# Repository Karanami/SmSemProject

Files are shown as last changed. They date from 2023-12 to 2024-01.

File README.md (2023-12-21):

# Piotr Lesicki 151052 - Line Follower

## General description
Line Follower - as it's name implies this robot will realise the task of following the line. 
The robot will consist of two motors, imu, line sensors (white/black color detectors), motor
encoders as well as an external data storage (flash/sd card) for data logging and of coures
it will also have an uC for general control.

## Hardware

### Motors & motor encoders
The robot will use a simple brushed motor with an extended shaft for the encoder feedback

### IMU
A six axis IMU will be used for data logging.

### line sensors
Basic refleted light detectors will be used for estimating where a black line on a white
background is.

### External data storage
A external storage in a form of a chip or a sd card will be used for logging

### uC
An STM32WB55RGVx will be used for the heart of the robot. It will also allow for a bluetooth
communication implementation to be included in the project, making the whole project smaller 
and more compact.

## Line Following task - regulator
The appropriate regulator is yet to be chosen

## Software

### RTOS 
For an easier implementation of software a fitting RTOS will be used. Azure RTOS will be used 
for that since it implements many robust sub-libraries allowing for light-weight aplications,
such as storage (file storage) drivers for external flash/sd cards or usb interfaces allowing
for on slave multiple devices implemantation and much more.
<br/> 

## Examples
- https://forbot.pl/blog/leksykon/robot-typu-linefollower
- https://www.jsumo.com/arduino-pid-based-line-follower-kit1

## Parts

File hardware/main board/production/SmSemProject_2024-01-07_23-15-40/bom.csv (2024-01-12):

Designator | Footprint | Quantity | Value | LCSC Part #
ANT1 | 74889302450 | 1 | 74889302450
C1, C2 | 0603 | 2 | 20pF
C10 | 0603 | 1 | 100pF
C11, C16, C19, C25, C26, C27, C28, C3, C30, C31, C4, C5, C9 | 0603 | 13 | 100nF
C13 | 0603 | 1 | 10uF
C14, C15, C18, C24 | 0603 | 4 | 4.7uF
C17, C29 | CP_Elec_5x4.5 | 2 | 100uF
C20 | 0603 | 1 | 0.3pF
C21 | 0603 | 1 | 0.8pF
C7 | 0603 | 1 | 10nF
C8 | 0603 | 1 | 1uF
D1, D3 | D_SOD-128 | 2 | RBS2LAM40CTR
D2, D4, D5, D6, D7, D8 | 0603 | 6 | LED_Small
F1, F2 | 1210 | 2 | 0.5A/16V
FL1 | DLF162500LT5028A1 | 1 | DLF162500LT-5028A1
H1, H2, H3, H4 | MountingHole_3.2mm_M3_Pad_Via | 4 | MountingHole_Pad
IC1 | QFN40P800X800X100-69N-D | 1 | STM32WB55RGV6
IC2, IC3 | SON50P200X200X80-9N | 2 | DRV8212PDSGR
IC4 | SON127P800X600X80-9N-D | 1 | W25N01GVZEIG
IC5 | LSM6DSLTR | 1 | LSM6DSLTR
IC6, IC7 | SOT-23-6 | 2 | SN74LVC1G18DBVRG4
J1, J2 | JST_SH_BM06B-SRSS-TB_1x06-1MP_P1.00mm_Vertical | 2 | JST-SH 01x06
J3 | JST_XH_B3B-XH-A_1x03_P2.50mm_Vertical | 1 | JST_XH_B3B
J4 | FTSH-107-XX-YYY-DV-K-A | 1 | FTSH-107-01-L-DV-K-A
J6 | USB4145030070C | 1 | USB4145-03-0070-C
J7 | Molex_200528-0100_1x10-1MP_P1.00mm_Horizontal | 1 | Conn_01x10
L1 | 1206 | 1 | 1mH
L2 | WE-PMI_080562 | 1 | 74479774222
L3 | 0603 | 1 | 2.7nH
R1 | 0603 | 1 | 1k
R10, R11, R12, R4, R5, R6, R7, R8, R9 | 0603 | 9 | 10k
R2, R3 | 0603 | 2 | 5.1k
U1 | SOT-223-3_TabPin2 | 1 | LM1117MP-3.3
U2 | SOT-23-6 | 1 | USBLC6-2SC6
Y1 | Crystal_SMD_3225-4Pin_3.2x2.5mm | 1 | X322516MLB4SI

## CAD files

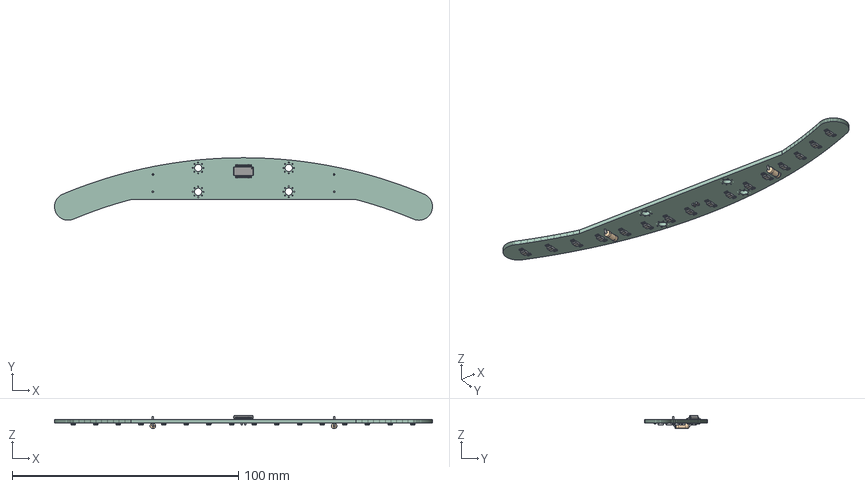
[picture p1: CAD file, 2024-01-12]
hardware/front board/SmSemProject-FrontBoard.step
166.9 x 27.6 x 5.95 mm
PCB

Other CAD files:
cad/podłoga1^całość.SLDPRT

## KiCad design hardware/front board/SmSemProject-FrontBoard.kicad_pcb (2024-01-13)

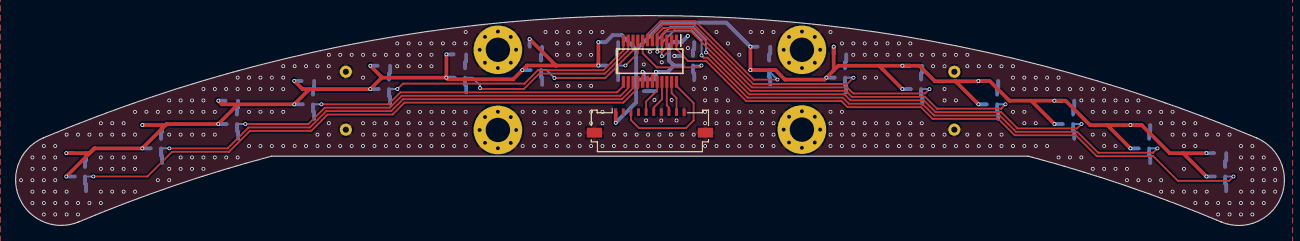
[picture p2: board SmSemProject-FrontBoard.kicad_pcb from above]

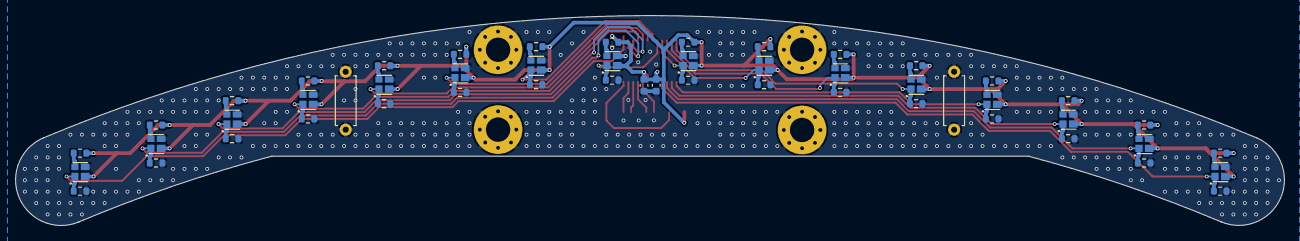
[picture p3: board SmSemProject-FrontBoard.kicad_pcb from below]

Board: 2 copper layers, 166.9 x 27.6 mm, 58 parts (52 on the bottom side), 39 nets.

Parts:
C1, C2: 100nF; C_0603_1608Metric
H1, H2, H3, H4: MountingHole_Pad; MountingHole_3.2mm_M3_Pad_Via
IC1, IC3, IC4, IC5, IC6, IC7, IC8, IC9, IC10, IC11, IC12, IC13, IC14, IC15, IC16, IC17: VCNT2020
IC2: MAX11643EEG+; SOP64P602X175-24N
J2: Conn_01x10_MountingPin; Molex_200528-0100_1x10-1MP_P1.00mm_Horizontal
R1, R3, R5, R7, R9, R11, R13, R15, R17, R19, R21, R23, R25, R27, R29, R31: 1k; R_0603_1608Metric
R2, R4, R6, R8, R10, R12, R14, R16, R18, R20, R22, R24, R26, R28, R30, R32: 100; R_0603_1608Metric
R33, R34: --; R_Axial_DIN0207_L6.3mm_D2.5mm_P7.62mm_Horizontal

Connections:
+3.3V: C1.2, C2.2, IC1.2, IC2.17 (REF), IC2.19 (VDD), IC3.2, IC4.2, IC5.2, IC6.2, IC7.2, IC8.2, IC9.2, IC10.2, IC11.2, IC12.2, IC13.2, IC14.2, IC15.2, IC16.2, IC17.2, J2.1, R2.2, R4.2, R6.2, R8.2, R10.2, R12.2, R14.2, R16.2, R18.2, R20.2, R22.2, R24.2, R26.2, R28.2, R30.2, R32.2
/OUT0: IC1.1, IC2.1 (AIN0), R1.1
/OUT1: IC2.2 (AIN1), IC3.1, R3.1
/OUT2: IC2.3 (AIN2), IC4.1, R5.1
/OUT3: IC2.4 (AIN3), IC5.1, R7.1
/OUT4: IC2.5 (AIN4), IC7.1, R11.1
/OUT5: IC2.6 (AIN5), IC8.1, R13.1
/OUT6: IC2.7 (AIN6), IC9.1, R15.1
/OUT7: IC2.8 (AIN7), IC6.1, R9.1
/OUT8: IC2.9 (AIN8), IC11.1, R19.1
/OUT9: IC2.10 (AIN9), IC12.1, R21.1
/OUT10: IC2.11 (AIN10), IC13.1, R23.1
/OUT11: IC2.12 (AIN11), IC10.1, R17.1
/OUT12: IC2.13 (AIN12), IC15.1, R27.1
/OUT13: IC2.14 (AIN13), IC16.1, R29.1
/OUT14: IC2.15 (AIN14), IC17.1, R31.1
/OUT15: IC2.16 (~CNVST/AIN15), IC14.1, R25.1
/SPI_CLK: IC2.21 (SCLK), J2.6
/SPI_EX_INT1: IC2.24 (~EOC), J2.3
/SPI_MISO: IC2.23 (DOUT), J2.9
/SPI_MOSI: IC2.22 (DIN), J2.8
/Sensor0/A: IC1.3 (A), R2.1
/Sensor1/A: IC3.3 (A), R4.1
/Sensor2/A: IC4.3 (A), R6.1
/Sensor3/A: IC5.3 (A), R8.1
/Sensor4/A: IC7.3 (A), R12.1
/Sensor5/A: IC8.3 (A), R14.1
/Sensor6/A: IC9.3 (A), R16.1
/Sensor7/A: IC6.3 (A), R10.1
/Sensor8/A: IC11.3 (A), R20.1
/Sensor9/A: IC12.3 (A), R22.1
/Sensor10/A: IC13.3 (A), R24.1
/Sensor11/A: IC10.3 (A), R18.1
/Sensor12/A: IC15.3 (A), R28.1
/Sensor13/A: IC16.3 (A), R30.1
/Sensor14/A: IC17.3 (A), R32.1
/Sensor15/A: IC14.3 (A), R26.1
/~SPI_EX1_CS: IC2.20 (~CS), J2.5
GND: C1.1, C2.1, H1.1, H2.1, H3.1, H4.1, IC1.4 (K), IC2.18 (GND), IC3.4 (K), IC4.4 (K), IC5.4 (K), IC6.4 (K), IC7.4 (K), IC8.4 (K), IC9.4 (K), IC10.4 (K), IC11.4 (K), IC12.4 (K), IC13.4 (K), IC14.4 (K), IC15.4 (K), IC16.4 (K), IC17.4 (K), J2.7, J2.10, J2.MP (MountPin), R1.2, R3.2, R5.2, R7.2, R9.2, R11.2, R13.2, R15.2, R17.2, R19.2, R21.2, R23.2, R25.2, R27.2, R29.2, R31.2, R33.1, R33.2, R34.1, R34.2

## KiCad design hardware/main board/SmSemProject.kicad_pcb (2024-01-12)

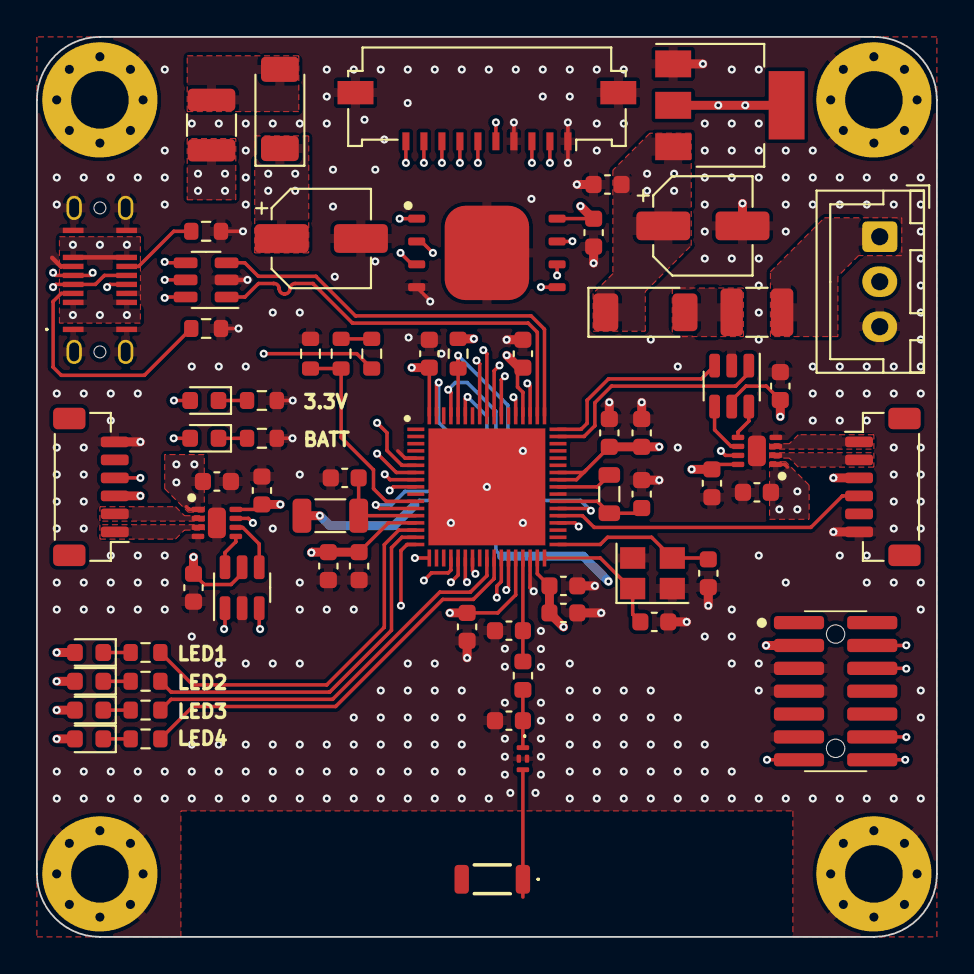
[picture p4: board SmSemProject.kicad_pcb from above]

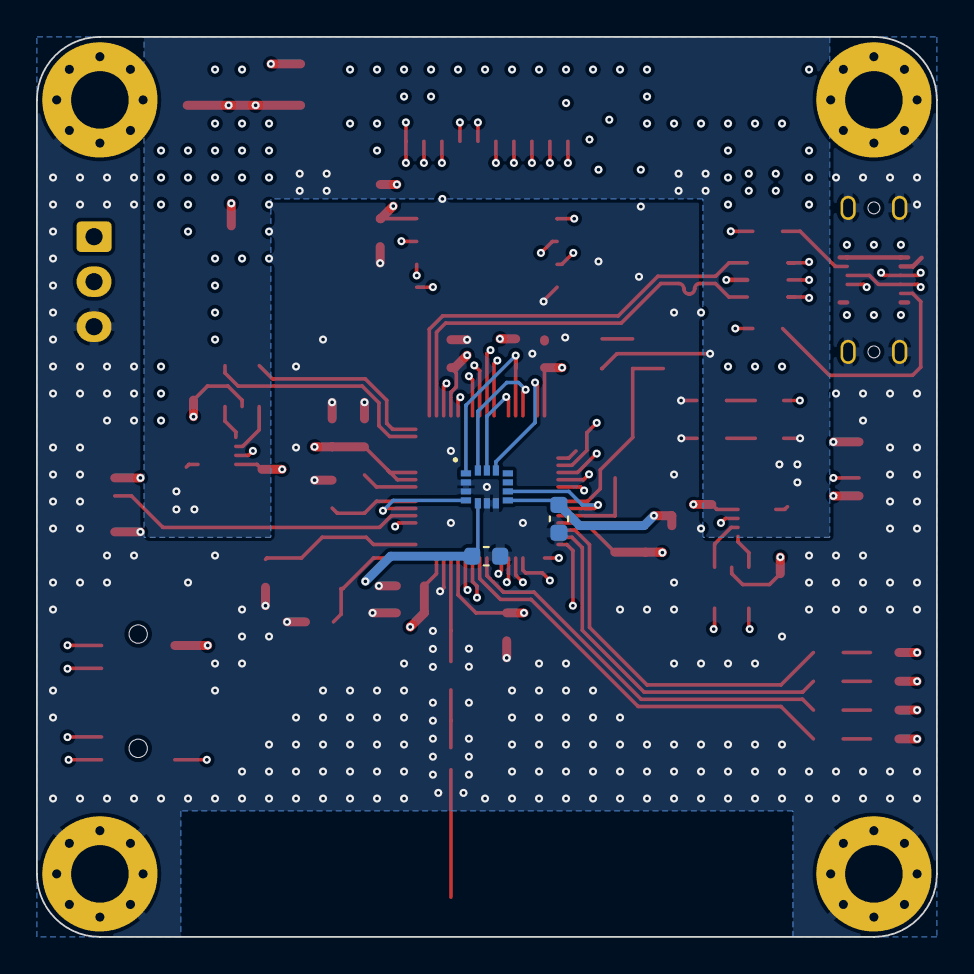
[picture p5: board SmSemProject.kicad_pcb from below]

Board: 8 copper layers, 50.0 x 50.0 mm, 74 parts (3 on the bottom side), 69 nets.

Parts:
ANT1: 74889302450
C1, C2: 20pF; C_0603_1608Metric
C3, C4, C5, C9, C11, C16, C19, C25, C26, C27, C28, C30, C31: 100nF; C_0603_1608Metric
C7: 10nF; C_0603_1608Metric
C8: 1uF; C_0603_1608Metric
C10: 100pF; C_0603_1608Metric
C13: 10uF; C_0603_1608Metric
C14, C15, C18, C24: 4.7uF; C_0603_1608Metric
C17, C29: 100uF; CP_Elec_5x4.5
C20: 0.3pF; C_0603_1608Metric
C21: 0.8pF; C_0603_1608Metric
D1, D3: RBS2LAM40CTR; D_SOD-128
D2, D4, D5, D6, D7, D8: LED_Small; LED_0603_1608Metric
F1, F2: 0.5A/16V; Fuse_1210_3225Metric
FL1: DLF162500LT-5028A1; DLF162500LT5028A1
H1, H2, H3, H4: MountingHole_Pad; MountingHole_3.2mm_M3_Pad_Via
IC1: STM32WB55RGV6; QFN40P800X800X100-69N-D
IC2, IC3: DRV8212PDSGR; SON50P200X200X80-9N
IC4: W25N01GVZEIG; SON127P800X600X80-9N-D
IC5: LSM6DSLTR
IC6, IC7: SN74LVC1G18DBVRG4; SOT-23-6
J1, J2: JST-SH 01x06; JST_SH_BM06B-SRSS-TB_1x06-1MP_P1.00mm_Vertical
J3: JST_XH_B3B; JST_XH_B3B-XH-A_1x03_P2.50mm_Vertical
J4: FTSH-107-01-L-DV-K-A; FTSH-107-XX-YYY-DV-K-A
J6: USB4145-03-0070-C; USB4145030070C
J7: Conn_01x10; Molex_200528-0100_1x10-1MP_P1.00mm_Horizontal
L1: 1mH; L_1206_3216Metric
L2: 74479774222; WE-PMI_080562
L3: 2.7nH; L_0603_1608Metric
R1: 1k; R_0603_1608Metric
R2, R3: 5.1k; R_0603_1608Metric
R4, R5, R6, R7, R8, R9, R10, R11, R12: 10k; R_0603_1608Metric
U1: LM1117MP-3.3; SOT-223-3_TabPin2
U2: USBLC6-2SC6; SOT-23-6
Y1: X322516MLB4SI; Crystal_SMD_3225-4Pin_3.2x2.5mm

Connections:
+3.3V: C3.2, C4.2, C5.2, C7.1, C8.1, C9.2, C10.2, C11.2, C15.1, C19.1, C25.1, C26.1, C27.2, C28.2, C30.1, C31.1, D2.2 (A), D4.2 (A), D5.2 (A), D6.2 (A), D7.2 (A), IC1.14 (VDDA), IC1.30 (VDD), IC1.33 (VDDRF), IC1.44 (VDDSMPS), IC1.45 (VDD), IC1.55 (VDDUSB), IC1.68 (VDD), IC2.8 (VCC), IC3.8 (VCC), IC4.8 (VCC), IC5.5 (VDDIO), IC5.8 (VDD), IC6.5 (VCC), IC7.5 (VCC), J1.3, J2.3, J4.3, J7.10, L1.1, R1.1, U1.2 (VO)
+BATT: C16.1, C17.1, C18.1, C24.1, C29.1, D1.1 (K), D3.1 (K), D8.2 (A), IC2.1 (VM), IC3.1 (VM), R9.2, U1.3 (VI)
/ANT_IN: ANT1.1 (FEED), FL1.3 (OUT)
/CONN_D+: J6.A6 (D+), J6.B6 (D+), U2.6 (I/O1)
/CONN_D-: J6.A7 (D-), J6.B7 (D-), U2.4 (I/O2)
/FLT_IN: C21.2, FL1.1 (IN), L3.2
/M_LEFT+: IC2.3 (OUT2), J2.1
/M_LEFT-: IC2.2 (OUT1), J2.2
/M_LEFT_A: IC1.9 (PC0), J2.4
/M_LEFT_DIRECTION: IC1.24 (PA9), IC7.1
/M_LEFT_PWM: IC1.23 (PA8), IC7.3
/M_RIGHT+: IC3.3 (OUT2), J1.1
/M_RIGHT-: IC3.2 (OUT1), J1.2
/M_RIGHT_A: IC1.39 (PB1), J1.4
/M_RIGHT_DIRECTION: IC1.50 (PC6), IC6.1
/M_RIGHT_PWM: IC1.51 (PA10), IC6.3
/Motor Control Left/PWMF: IC2.6 (IN1), IC7.4
/Motor Control Left/PWMR: IC2.5 (IN2), IC7.6
/Motor Control Left/~SLEEP: IC1.38 (PB0), IC2.7 (~SLEEP), IC3.7 (~SLEEP)
/Motor Control Right/PWMF: IC3.6 (IN1), IC6.4
/Motor Control Right/PWMR: IC3.5 (IN2), IC6.6
/SPI_CLK: IC1.63 (PB3), IC5.13 (SCL), J7.5
/SPI_EX_INT1: IC1.60 (PC12), J7.8
/SPI_EX_INT2: IC1.61 (PD0), J7.9
/SPI_MISO: IC1.64 (PB4), IC5.1 (SDO/SA0), J7.2, R1.2
/SPI_MOSI: IC1.65 (PB5), IC5.14 (SDI/SDA), J7.3
/VBUS: F2.1, J6.A4 (VBUS), J6.A9 (VBUS), J6.B4 (VBUS), J6.B9 (VBUS), U2.5 (VBUS)
/VBUSFUSE: D3.2 (A), F2.2
/VCONN: F1.2, J3.1
/VFUSE: D1.2 (A), F1.1
/uC/ANT_OUT: C20.1, IC1.31 (RF1), L3.1
/uC/D+: IC1.53 (PA12), U2.1 (I/O1)
/uC/D-: IC1.52 (PA11), U2.3 (I/O2)
/uC/IMU_INT1: IC1.12 (PC3), IC5.9 (INT2)
/uC/IMU_INT2: IC1.40 (PE4), IC5.4 (INT1)
/uC/LED1: IC1.15 (PA0), R5.1
/uC/LED2: IC1.16 (PA1), R6.1
/uC/LED3: IC1.26 (PC5), R7.1
/uC/LED4: IC1.27 (PB2), R8.1
/uC/OSC_IN: C1.2, IC1.35 (OSC_IN), Y1.3
/uC/OSC_OUT: C2.1, IC1.34 (OSC_OUT), Y1.1
/uC/QSPI_CLK: IC1.18 (PA3), IC4.6 (CLK)
/uC/QSPI_IO0: IC1.7 (PB9), IC4.5 (DI(IO0))
/uC/QSPI_IO1: IC1.6 (PB8), IC4.2 (DO(IO1))
/uC/QSPI_IO2: IC1.22 (PA7), IC4.3 (~WP(IO2))
/uC/QSPI_IO3: IC1.21 (PA6), IC4.7 (~HOLD(IO3))
/uC/SWCLK: IC1.56 (PA14), J4.6
/uC/SWDIO: IC1.54 (PA13), J4.4
/uC/UART_RX: IC1.28 (PB10), J4.13
/uC/UART_TX: IC1.29 (PB11), J4.14
/uC/VBAT: IC1.11 (PC2), R10.2, R11.1
/uC/VFBSMPS: C14.1, IC1.41 (VFBSMPS), L2.2
/uC/VLXSMPS: IC1.43 (VLXSMPS), L2.1
/uC/VREF+: C13.2, IC1.13 (VREF+), L1.2
/uC/~QSPI_CS: IC1.17 (PA2), IC4.1 (~CS)
/uC/~RST: IC1.8 (~RST), J4.12
/uC/~SPI_IMU_CS: IC1.67 (PB7), IC5.12 (~CS)
/~SPI_EX1_CS: IC1.58 (PC10), J7.6
/~SPI_EX2_CS: IC1.59 (PC11), J7.7
GND: C1.1, C2.2, C3.1, C4.1, C5.1, C7.2, C8.2, C9.1, C10.1, C11.1, C13.1, C14.2, C15.2, C16.2, C17.2, C18.2, C19.2, C20.2, C21.1, C24.2, C25.2, C26.2, C27.1, C28.1, C29.2, C30.2, C31.2, FL1.2 (GND), FL1.4 (GND), H1.1, H2.1, H3.1, H4.1, IC1.5 (PH3-BOOT0), IC1.32 (VSSRF), IC1.42 (VSSSMPS), IC1.69 (EP), IC2.4 (GND), IC2.9 (EP), IC3.4 (GND), IC3.9 (EP), IC4.4 (GND), IC4.9 (EP), IC5.2 (SDX), IC5.3 (SCX), IC5.6 (GND), IC5.7 (GND), IC6.2 (GND), IC7.2 (GND), J1.6, J2.6, J3.3, J4.5, J4.7, J4.11, J6.A1 (GND), J6.A8 (SBU1), J6.A12 (GND), J6.B1 (GND), J6.B8 (SBU2), J6.B12 (GND), J6.MH (SHIELD), J7.1, J7.4, J7.MP (MountPin), R2.2, R3.2, R4.1, R10.1, R12.1, U1.1 (GND), U2.2 (GND), Y1.2, Y1.4
unnamed: D2.1 (K), R4.2
unnamed: D4.1 (K), R5.2
unnamed: D5.1 (K), R6.2
unnamed: D6.1 (K), R7.2
unnamed: D7.1 (K), R8.2
unnamed: D8.1 (K), R12.2
unnamed: J6.A5 (CC1), R2.1
unnamed: J6.B5 (CC2), R3.1
unnamed: R9.1, R11.2

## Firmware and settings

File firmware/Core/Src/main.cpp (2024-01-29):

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
/* Includes ------------------------------------------------------------------*/
#include "main.h"
#include "cmsis_os.h"
#include "adc.h"
#include "dma.h"
#include "ipcc.h"
#include "lptim.h"
#include "usart.h"
#include "memorymap.h"
#include "quadspi.h"
#include "rf.h"
#include "rtc.h"
#include "spi.h"
#include "tim.h"
#include "usb.h"
#include "gpio.h"

/* USER CODE BEGIN Includes */
//#include "FreeRTOS.h"
#include <FreeRTOS.h>
#include <app_freertos.h>
#include "common.hpp"
#include "max11643.hpp"
#include "lsm6dsl.hpp"
#include "extern_vars.hpp"
/* USER CODE END Includes */


/* USER CODE BEGIN PV */

GpioOut led1 = GPIO_OUT(LED1, true);
GpioOut led2 = GPIO_OUT(LED2, true);
GpioOut led3 = GPIO_OUT(LED3, true);
GpioOut led4 = GPIO_OUT(LED4, true);

GpioOut nm_sleep 			= GPIO_OUT(NM_SLEEP, true);
GpioOut m_right_direction 	= GPIO_OUT(M_RIGHT_DIRECTION, true);
GpioOut m_left_direction 	= GPIO_OUT(M_LEFT_DIRECTION, true);

GpioOut spi_imu_ncs		= GPIO_OUT(SPI_IMU_NCS, true);
GpioIn spi_imu_int1 	= GPIO_IN(SPI_IMU_INT1, true);
GpioIn spi_imu_int2 	= GPIO_IN(SPI_IMU_INT2, true);

GpioOut spi_ex_ncs1 = GPIO_OUT(SPI_EX_NCS1, true);
GpioOut spi_ex_ncs2 = GPIO_OUT(SPI_EX_NCS2, true);
GpioIn spi_ex_int1 	= GPIO_IN(SPI_EX_INT1, true);
//GpioIn spi_ex_int2 	= GPIO_IN(SPI_EX_INT2, true);

constexpr float encoder_ratio = 1.f / 6.f / 10.f;
Encoder left_encoder(&hlptim1, encoder_ratio);
Encoder right_encoder(&hlptim2, encoder_ratio);

PwmOut left_speed_ctrl(&htim1, PwmOutCh::_1);
PwmOut right_speed_ctrl(&htim1, PwmOutCh::_3);

Max11643 front_adc(&hspi1, &spi_ex_ncs1, &spi_ex_int1);

Lsm6dsl imu(&hspi1, &spi_imu_ncs, &spi_imu_int1, &spi_imu_int2);

float anglspd1;
float anglspd2;

/* USER CODE END PV */

void SystemClock_Config(void);
void PeriphCommonClock_Config(void);
void MX_FREERTOS_Init(void);
/**
  * @brief  The application entry point.
  * @retval int
  */
int main(void)
{
  /* MCU Configuration--------------------------------------------------------*/

  /* Reset of all peripherals, Initializes the Flash interface and the Systick. */
  HAL_Init();
  /* Config code for STM32_WPAN (HSE Tuning must be done before system clock configuration) */
  MX_APPE_Config();

  /* Configure the system clock */
  SystemClock_Config();

/* Configure the peripherals common clocks */
  PeriphCommonClock_Config();

  /* IPCC initialisation */
  MX_IPCC_Init();

  /* Initialize all configured peripherals */
  MX_GPIO_Init();
  MX_DMA_Init();
  MX_TIM1_Init();
  MX_USB_PCD_Init();
  MX_ADC1_Init();
  MX_LPTIM2_Init();
  MX_QUADSPI_Init();
  MX_SPI1_Init();
  MX_LPUART1_UART_Init();
  MX_RTC_Init();
  MX_LPTIM1_Init();
  MX_RF_Init();
  /* Init scheduler */
  osKernelInitialize();
  /* Init code for STM32_WPAN */
  MX_APPE_Init();

  /* Call init function for freertos objects (in freertos.c) */
  MX_FREERTOS_Init();

  /* Start scheduler */
  osKernelStart();

  /* We should never get here as control is now taken by the scheduler */
  /* Infinite loop */
  /* USER CODE BEGIN WHILE */
  while (1)
  {
    /* USER CODE END WHILE */

    /* USER CODE BEGIN 3 */
  }
  /* USER CODE END 3 */
}

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
/* USER CODE BEGIN 4 */
void HAL_GPIO_EXIT_Callback(uint16_t GPIO_Pin)
{
	if(GPIO_Pin == 0)
	{
		led2.toggle();
	}
}
/* USER CODE END 4 */

/**
  * @brief  Period elapsed callback in non blocking mode
  * @note   This function is called  when TIM17 interrupt took place, inside
  * HAL_TIM_IRQHandler(). It makes a direct call to HAL_IncTick() to increment
  * a global variable "uwTick" used as application time base.
  * @param  htim : TIM handle
  * @retval None
  */
void HAL_TIM_PeriodElapsedCallback(TIM_HandleTypeDef *htim)
{
  if (htim->Instance == TIM17) {
    HAL_IncTick();
  }
}

/**
  * @brief  This function is executed in case of error occurrence.
  * @retval None
  */
void Error_Handler(void)
{
  /* USER CODE BEGIN Error_Handler_Debug */
  /* User can add his own implementation to report the HAL error return state */
  __disable_irq();
  while (1)
  {
  }
  /* USER CODE END Error_Handler_Debug */
}

#ifdef  USE_FULL_ASSERT
/**
  * @brief  Reports the name of the source file and the source line number
  *         where the assert_param error has occurred.
  * @param  file: pointer to the source file name
  * @param  line: assert_param error line source number
  * @retval None
  */
void assert_failed(uint8_t *file, uint32_t line)
{
  /* USER CODE BEGIN 6 */
  /* User can add his own implementation to report the file name and line number,
     ex: printf("Wrong parameters value: file %s on line %d\r\n", file, line) */
  /* USER CODE END 6 */
}
#endif /* USE_FULL_ASSERT */

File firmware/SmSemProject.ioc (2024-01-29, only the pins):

Mcu.UserName=STM32WB55RGVx
PA0.GPIO_Label=LED1
PA0.Signal=GPIO_Output
PA1.GPIO_Label=LED2
PA1.Signal=GPIO_Output
PA10.GPIO_Label=M_RIGHT_PWM
PA10.Signal=S_TIM1_CH3
PA11.Signal=USB_DM
PA12.Signal=USB_DP
PA13.Signal=SYS_JTMS-SWDIO
PA14.Signal=SYS_JTCK-SWCLK
PA2.GPIO_Label=QSPI_NCS
PA2.Signal=QUADSPI_BK1_NCS
PA3.GPIO_Label=QSPI_CLK
PA3.Signal=QUADSPI_CLK
PA6.GPIO_Label=QSPI_IO3
PA6.Signal=QUADSPI_BK1_IO3
PA7.GPIO_Label=QSPI_IO2
PA7.Signal=QUADSPI_BK1_IO2
PA8.GPIO_Label=M_LEFT_PWM
PA8.Signal=S_TIM1_CH1
PA9.GPIO_Label=M_LEFT_DIRECTION
PA9.Signal=GPIO_Output
PB0.GPIO_Label=NM_SLEEP
PB0.Signal=GPIO_Output
PB1.GPIO_Label=M_RIGHT_A
PB1.Signal=LPTIM2_IN1
PB10.GPIO_Label=UART_RX
PB10.Signal=LPUART1_RX
PB11.GPIO_Label=UART_TX
PB11.Signal=LPUART1_TX
PB2.GPIO_Label=LED4
PB2.Signal=GPIO_Output
PB3.GPIO_Label=SPI_SCK
PB3.Signal=SPI1_SCK
PB4.GPIO_Label=SPI_MOSI
PB4.Signal=SPI1_MISO
PB5.GPIO_Label=SPI_MISO
PB5.Signal=SPI1_MOSI
PB7.GPIO_Label=SPI_IMU_NCS
PB7.Signal=GPIO_Output
PB8.GPIO_Label=QSPI_IO1
PB8.Signal=QUADSPI_BK1_IO1
PB9.GPIO_Label=QSPI_IO0
PB9.Signal=QUADSPI_BK1_IO0
PC0.GPIO_Label=M_LEFT_PWM
PC0.Signal=LPTIM1_IN1
PC10.GPIO_Label=SPI_EX_NCS1
PC10.Signal=GPIO_Output
PC11.GPIO_Label=SPI_EX_NCS2
PC11.Signal=GPIO_Output
PC12.GPIO_Label=SPI_EX_INT1
PC12.Signal=GPXTI12
PC2.GPIO_Label=VBAT
PC2.Signal=ADCx_IN3
PC3.GPIO_Label=SPI_IMU_INT1
PC3.Signal=GPXTI3
PC5.GPIO_Label=LED3
PC5.Signal=GPIO_Output
PC6.GPIO_Label=M_RIGHT_DIRECTION
PC6.Signal=GPIO_Output
PD0.GPIO_Label=SPI_EX_INT2
PD0.Signal=GPXTI0
PE4.GPIO_Label=SPI_IMU_INT2
PE4.Signal=GPXTI4

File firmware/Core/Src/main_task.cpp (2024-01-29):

/* USER CODE BEGIN Header */
/**
  ******************************************************************************
  * @file           : main_task.cpp
  * @brief          : handles mission choosing and activation as well
  * 				  as other task's suspension and activation
  ******************************************************************************
  */

#include "FreeRTOS.h"
#include "task.h"
#include "extern_vars.hpp"
#include "app_freertos.h"
#include "main.h"
#include "cstring"
#include "algorithm"
#include "usart.h"
#include "array"

volatile static bool it_state;

static float duty_kek = 0.f;
char cmd[8] = { 0 };

char data [128] = { 0 };

void mainTaskEntry(void *argument)
{
	// engine init
	right_encoder.init();
	right_speed_ctrl.init();
	left_encoder.init();
	left_speed_ctrl.init();
	nm_sleep.off();

	// front init
	front_adc.init();

	//other init
	led1.off();
	led2.off();
	led3.off();
	led4.off();

	HAL_UART_Receive_IT(&hlpuart1, (uint8_t*)cmd, 5);

	//int i = 0;
	while(true)
	{
		size_t size = sprintf(data, "speed: %i, set_speed: %i\n\r", (uint32_t)speed, (uint32_t)set_speed);
		HAL_UART_Transmit(&hlpuart1, (uint8_t*)data, strlen(data), 100);
		left_speed_ctrl.setDuty(duty_kek);
		//it_state = spi_ex_int1.read();

		front_adc.init();
		front_adc.requestData();
		vTaskDelay(1);
		front_adc.readData();

		static std::array<float, 16> coefs = { -8, -7, -6, -5, -4, -3, -2, -1, 1, 2, 3, 4, 5, 6, 7, 8 };
		follow_deviation = 0;
		for(size_t i = 0; i < 16; i++)
		{
			uint16_t buff = (uint16_t)(front_adc.data()[i * 2]) << 8 | (uint16_t)(front_adc.data()[i * 2 + 1]);
			if (buff > 32)
			{
				follow_deviation += coefs[i];
			}
		}

		front_adc.data();

		led1.toggle();
		vTaskDelay(100);
	}
}

void HAL_UART_RxCpltCallback(UART_HandleTypeDef *huart)
{
	if(cmd[0] == 's' || cmd[0] == 'S')
	{
		int set = atoi(cmd + 1);
		set = std::clamp(set, 500, 3500);
		set_speed = (float)set;
	}
	HAL_UART_Receive_IT(&hlpuart1, (uint8_t*)cmd, 5);
}

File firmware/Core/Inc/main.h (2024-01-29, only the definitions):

#define QSPI_IO1_Pin LL_GPIO_PIN_8
#define QSPI_IO1_GPIO_Port GPIOB
#define QSPI_IO0_Pin LL_GPIO_PIN_9
#define QSPI_IO0_GPIO_Port GPIOB
#define M_LEFT_PWM_Pin LL_GPIO_PIN_0
#define M_LEFT_PWM_GPIO_Port GPIOC
#define VBAT_Pin LL_GPIO_PIN_2
#define VBAT_GPIO_Port GPIOC
#define SPI_IMU_INT1_Pin LL_GPIO_PIN_3
#define SPI_IMU_INT1_GPIO_Port GPIOC
#define LED1_Pin LL_GPIO_PIN_0
#define LED1_GPIO_Port GPIOA
#define LED2_Pin LL_GPIO_PIN_1
#define LED2_GPIO_Port GPIOA
#define QSPI_NCS_Pin LL_GPIO_PIN_2
#define QSPI_NCS_GPIO_Port GPIOA
#define QSPI_CLK_Pin LL_GPIO_PIN_3
#define QSPI_CLK_GPIO_Port GPIOA
#define QSPI_IO3_Pin LL_GPIO_PIN_6
#define QSPI_IO3_GPIO_Port GPIOA
#define QSPI_IO2_Pin LL_GPIO_PIN_7
#define QSPI_IO2_GPIO_Port GPIOA
#define M_LEFT_PWMA8_Pin LL_GPIO_PIN_8
#define M_LEFT_PWMA8_GPIO_Port GPIOA
#define M_LEFT_DIRECTION_Pin LL_GPIO_PIN_9
#define M_LEFT_DIRECTION_GPIO_Port GPIOA
#define LED3_Pin LL_GPIO_PIN_5
#define LED3_GPIO_Port GPIOC
#define LED4_Pin LL_GPIO_PIN_2
#define LED4_GPIO_Port GPIOB
#define UART_RX_Pin LL_GPIO_PIN_10
#define UART_RX_GPIO_Port GPIOB
#define UART_TX_Pin LL_GPIO_PIN_11
#define UART_TX_GPIO_Port GPIOB
#define NM_SLEEP_Pin LL_GPIO_PIN_0
#define NM_SLEEP_GPIO_Port GPIOB
#define M_RIGHT_A_Pin LL_GPIO_PIN_1
#define M_RIGHT_A_GPIO_Port GPIOB
#define SPI_IMU_INT2_Pin LL_GPIO_PIN_4
#define SPI_IMU_INT2_GPIO_Port GPIOE
#define M_RIGHT_DIRECTION_Pin LL_GPIO_PIN_6
#define M_RIGHT_DIRECTION_GPIO_Port GPIOC
#define M_RIGHT_PWM_Pin LL_GPIO_PIN_10
#define M_RIGHT_PWM_GPIO_Port GPIOA
#define SPI_EX_NCS1_Pin LL_GPIO_PIN_10
#define SPI_EX_NCS1_GPIO_Port GPIOC
#define SPI_EX_NCS2_Pin LL_GPIO_PIN_11
#define SPI_EX_NCS2_GPIO_Port GPIOC
#define SPI_EX_INT1_Pin LL_GPIO_PIN_12
#define SPI_EX_INT1_GPIO_Port GPIOC
#define SPI_EX_INT2_Pin LL_GPIO_PIN_0
#define SPI_EX_INT2_GPIO_Port GPIOD
#define SPI_SCK_Pin LL_GPIO_PIN_3
#define SPI_SCK_GPIO_Port GPIOB
#define SPI_MOSI_Pin LL_GPIO_PIN_4
#define SPI_MOSI_GPIO_Port GPIOB
#define SPI_MISO_Pin LL_GPIO_PIN_5
#define SPI_MISO_GPIO_Port GPIOB
#define SPI_IMU_NCS_Pin LL_GPIO_PIN_7
#define SPI_IMU_NCS_GPIO_Port GPIOB

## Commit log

2024-01-04 schematic progress has been made
    [MotorControl.kicad_sch, PowerDistribution.kicad_sch, SmSemProject.kicad_pcb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]
2024-01-05 main board done, added front board projec
    [MotorControl.kicad_sch, SmSemProject-FrontBoard.kicad_pcb, SmSemProject-FrontBoard.kicad_sch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]
2024-01-06 front board schematic done
    [Sensor.kicad_sch, SmSemProject-FrontBoard.kicad_pcb, SmSemProject-FrontBoard.kicad_sch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]
2024-01-06 front board layout & routing mostly done
    [Sensor.kicad_sch, SmSemProject-FrontBoard.kicad_pcb, SmSemProject-FrontBoard.kicad_sch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]
2024-01-07 all layouts and routings done
    [MotorControl.kicad_sch, SmSemProject-FrontBoard.kicad_pcb, SmSemProject.kicad_pcb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]
2024-01-07 tuned lenghts of signals with higher frequencies
    [SmSemProject.kicad_pcb]
2024-01-12 firmware - added common classes
    [MotorControl.kicad_sch, Sensor.kicad_sch, SmSemProject-FrontBoard.kicad_pcb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]

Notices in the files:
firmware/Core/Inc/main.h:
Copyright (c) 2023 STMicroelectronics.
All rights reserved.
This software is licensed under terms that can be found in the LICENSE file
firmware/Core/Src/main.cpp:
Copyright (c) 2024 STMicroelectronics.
